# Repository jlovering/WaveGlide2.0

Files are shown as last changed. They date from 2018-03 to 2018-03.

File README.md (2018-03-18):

# WaveGlide 2.0

This project extends the work by [Nortd Labs](http://nortd.github.io/WaveGlide/). It seeks to take their work and simpify the board design.

This is intended as an Open Source Hardware ([OSHWA](https://www.oshwa.org)) project and will attempt to follow the OSHWA [Best Practices](https://www.oshwa.org/sharing-best-practices/). All parts of this design are released under CC-BY-SA 4.0 unless otherwise noted. See LICENSE.md for more details.

# Status
This project is in it's infancy. Current status is "Design Incomplete"

## Detailed Status
* EE Design
  * Component Selection: Complete
  * Schematic Capture: Incomplete
    * Power domains remain
  * Board Layout: Incomplete
    * Initial Floorplaning Started
  * Board Validation: Incomplete

* ME Design
  * ECAD Parts: Mostly Complete
  * MCAD Parts: Not Started
  * Assempbly Design: Not Started

 * Software Design: Not Started

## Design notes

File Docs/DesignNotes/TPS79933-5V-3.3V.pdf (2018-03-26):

## WEBENCH ® Design Report

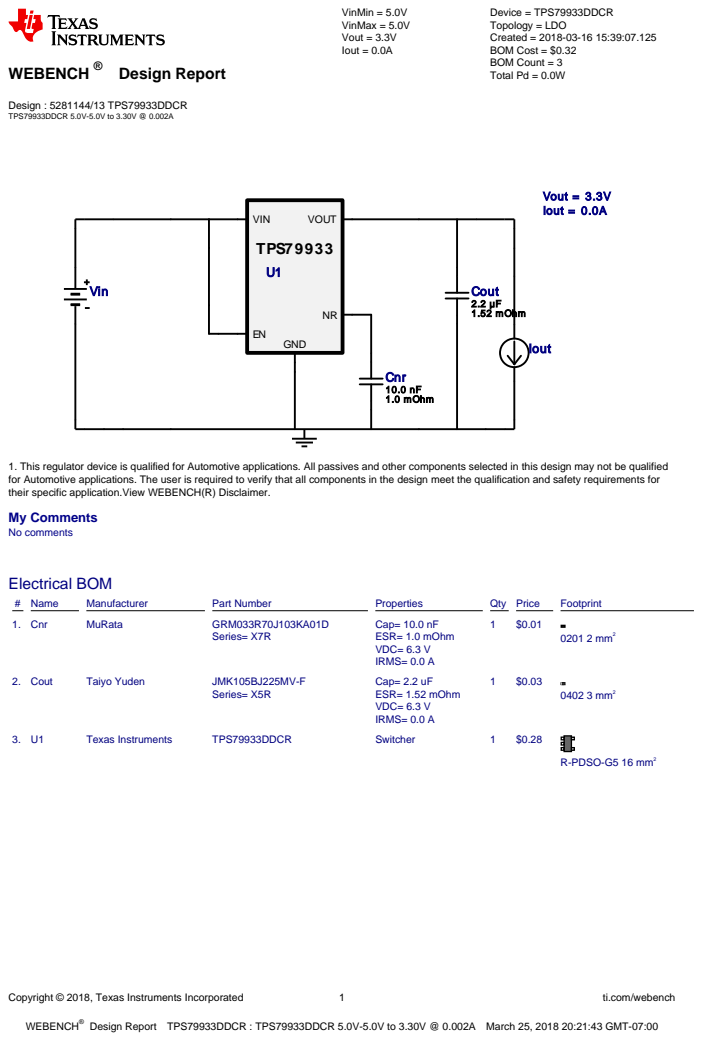
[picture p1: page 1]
Copyright © 2018, Texas Instruments Incorporated; ti.com/webench; WEBENCH®; Design : 5281144/13 TPS79933DDCR TPS79933DDCR 5.0V-5.0V to 3.30V @ 0.002A; VinMin = 5.0V VinMax = 5.0V Vout = 3.3V Iout = 0.0A; Device = TPS79933DDCR Topology = LDO Created = 2018-03-16 15:39:07.125 BOM Cost = $0.32 BOM Count = 3 Total Pd = 0.0W; Cnr 10.0 nF 1.0 mOhm; Cout 2.2 µF 1.52 mOhm; TPS79933; VIN; GND; VOUT; Vout = 3.3V Iout = 0.0A; Vin; Iout; Electrical BOM; # Name; Manufacturer; Part Number; Properties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

1. This regulator device is qualified for Automotive applications. All passives and other components selected in this design may not be qualified
for Automotive applications. The user is required to verify that all components in the design meet the qualification and safety requirements for
their specific application.View WEBENCH(R) Disclaimer.
My Comments
No comments

Design Report TPS79933DDCR : TPS79933DDCR 5.0V-5.0V to 3.30V @ 0.002A March 25, 2018 20:21:43 GMT-07:00

Design

Copyright © 2018, Texas Instruments Incorporated | 2 | ti.com/webench

Iin Avg

Vin= 5.0V

0.00025 0.00050 0.00075 0.00100 0.00125 0.00150 0.00175 0.00200 Output Current (A)

0.00000

0.00025

0.00050

0.00075

0.00100

0.00125

0.00150

0.00175

0.00200

Iin Avg(A)

Efficiency

Vin= 5.0V

0.00025 0.00050 0.00075 0.00100 0.00125 0.00150 0.00175 0.00200 Output Current (A)

45.0

47.5

50.0

52.5

55.0

57.5

60.0

62.5

65.0

Efficiency(%)

IC Pd

Vin= 5.0V

0.00025 0.00050 0.00075 0.00100 0.00125 0.00150 0.00175 0.00200 Output Current (A)

0.00025

0.00050

0.00075

0.00100

0.00125

0.00150

0.00175

0.00200

0.00225

0.00250

0.00275

0.00300

0.00325

0.00350

0.00375

IC Pd(W)

Total Pd

Vin= 5.0V

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

0.00025

0.00050

0.00075

0.00100

0.00125

0.00150

0.00175

0.00200

0.00225

0.00250

0.00275

0.00300

0.00325

0.00350

0.00375

Total Pd(W)

Pout

Vin= 5.0V

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

0.0000

0.0005

0.0010

0.0015

0.0020

0.0025

0.0030

0.0035

0.0040

0.0045

0.0050

0.0055

0.0060

0.0065

Pout(W)

IC Tj

Vin= 5.0V

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

30.05

30.10

30.15

30.20

30.25

30.30

30.35

30.40

30.45

30.50

30.55

30.60

30.65

30.70

30.75

30.80

IC Tj(degC)

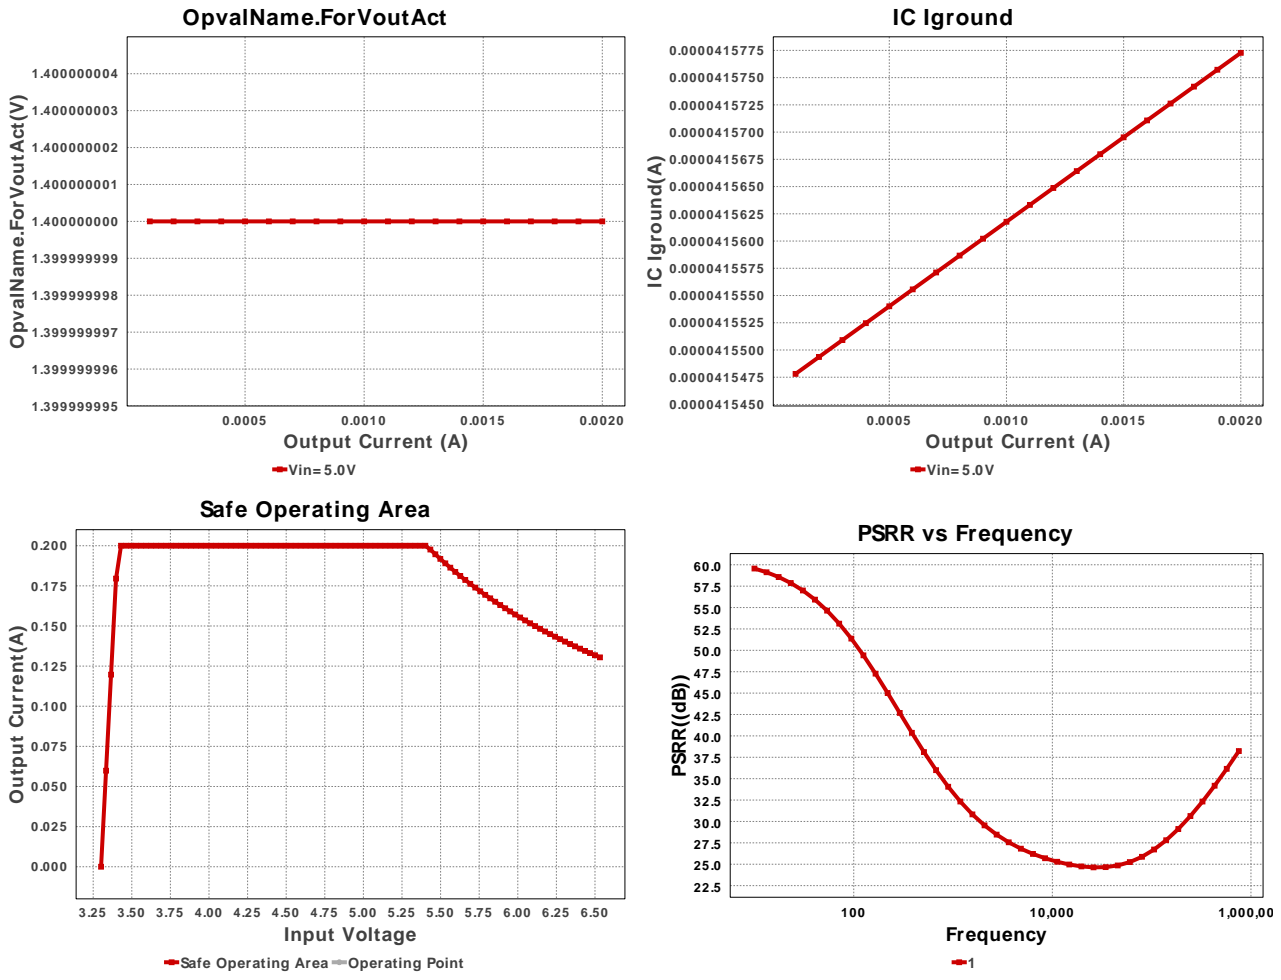
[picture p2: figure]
OpvalName.ForVoutAct; Vin= 5.0V; 0.0020 Output Current (A); OpvalName.ForVoutAct(V); IC Iground; IC Iground(A); Safe Operating Area; Safe Operating Area Operating Point; Input Voltage; Output Current(A); PSRR vs Frequency; 1,000,000 Frequency; PSRR((dB))

Copyright © 2018, Texas Instruments Incorporated | 3 | ti.com/webench

3.25 3.50 3.75 4.00 4.25 4.50 4.75 5.00 5.25 5.50 5.75 6.00 6.25 6.50

## Operating Values

# | Name | Value | Category | Description

1. IC Iground | 41.577 µA | Current | IC ground current
2. Iin Avg | 2.042 mA | Current | Average input current
3. BOM Count | 3 | General | Total Design BOM count
4. FootPrint | 21.0 mm² | General | Total Foot Print Area of BOM components
5. IC Tolerance | 66.0 mV | General | IC Feedback Tolerance
6. Output Noise RMS | 6.93 µV | General | Noise RMS
7. Pout | 6.6 mW | General | Total output power
8. Total BOM | $0.32 | General | Total BOM Cost
9. Efficiency | 64.656 % | Op Point | Steady state efficiency
10. IC Tj | 30.813 degC | Op Point | IC junction temperature
11. ICThetaJA | 225.3 degC/W | Op Point | IC junction-to-ambient thermal resistance
12. IOUT_OP | 2.0 mA | Op Point | Iout operating point
13. Input Ripple Frequency 100.0 kHz | Op Point | Input Source Ripple Frequency for PSRR Calculation
14. PSRR est. | -26.531 dB | Op Point | Power Supply Rejection Ratio estimated
15. VIN_OP | 5.0 V | Op Point | Vin operating point
16. Vin p-p | 50.0 mV | Op Point | Input Source ripple voltage
17. Vout OP | 3.3 V | Op Point | Operational Output Voltage
18. Vout Tolerance | 2.0 % | Op Point | Vout Tolerance based on IC Tolerance (no load) and voltage divider
| | | | resistors if applicable
19. Vout p-p | 2.357 mV | Op Point | Peak-to-peak output ripple voltage
20. IC Pd | 3.608 mW | Power | IC power dissipation
21. Total Pd | 3.608 mW | Power | Total Power Dissipation
22. Vout Act | 1.4 V | Achieved Vout with feedback resistor pair

## Design Inputs

# | Name | Value | Description

1. Iout | 2.0 m | Maximum Output Current
2. VinMax | 5.0 | Maximum input voltage
3. VinMin | 5.0 | Minimum input voltage
4. Vout | 3.3 | Output Voltage

Copyright © 2018, Texas Instruments Incorporated | 4 | ti.com/webench
# | Name | Value | Description

5. base_pn | TPS79933 | Base Product Number
6. source | DC | Input Source Type
7. Ta | 30.0 | Ambient temperature

## Design Assistance

1. TPS79933 Product Folder : http://www.ti.com/product/tps799 : contains the data sheet and other resources.

Texas Instruments' WEBENCH simulation tools attempt to recreate the performance of a substantially equivalent physical implementation
of the design. Simulations are created using Texas Instruments' published specifications as well as the published specifications of other device manufacturers. While Texas Instruments does update this information periodically, this information may not be current at the time the simulation is built. Texas Instruments does not warrant the accuracy or completeness of the specifications or any information contained therein. Texas Instruments does not warrant that any designs or recommended parts will meet the specifications you entered, will be suitable for your application or fit for any particular purpose, or will operate as shown in the simulation in a physical implementation. Texas Instruments does not warrant that the designs are production worthy.
You should completely validate and test your design implementation to confirm the system functionality for your application prior to production.
Use of Texas Instruments' WEBENCH simulation tools is subject to Texas Instruments' Site Terms and Conditions of Use. (http://www.ti.com/corp/docs/legal/termsofuse.shtml) Prototype boards based on WEBENCH created designs are provided AS IS without warranty of any kind for evaluation and testing purposes and are subject to the terms of the Evaluation License Agreement. (http://www.ti.com/corp/docs/legal/termsofuse_estore.shtml)

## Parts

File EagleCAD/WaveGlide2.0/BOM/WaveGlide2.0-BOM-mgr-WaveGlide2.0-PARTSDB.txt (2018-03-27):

Mfg Part Num	Mfg Name	VID	Vendor Part Num	Description	Pkg Code
N/A	N/A	DO NOT PLACE	DO NOT PLACE	*	*
N/A	N/A	TO BE DETERMINED	TO BE DETERMINED	*	*
ANY	ANY	ANY	ANY	ANY PART MATCHING	*
08053C104JAZ2A	AVX	TO BE DETERMINED	TO BE DETERMINED	CAP CER 0.1UF 25V X7R 0805	0805
GCM2195C1H103JA16D	MuRata	TO BE DETERMINED	TO BE DETERMINED	CAP CER 10000PF 50V C0G/NP0 0805	0805
GRM219R61A106KE44D	MuRata	TO BE DETERMINED	TO BE DETERMINED	CAP CER 10UF 10V X5R 0805	0805
CC0805KRX7R8BB104	Yageo America	TO BE DETERMINED	TO BE DETERMINED	CAP CER 0.1UF 25V X7R 0805	0805
GRM32ER61C226ME20L	MuRata	TO BE DETERMINED	TO BE DETERMINED	CAP CER 22UF 16V X5R 1210	1210
GRM155R60J223KA01D	MuRata	TO BE DETERMINED	TO BE DETERMINED	CAP CER 0.022UF 6.3V X5R 0402	0402
MBRD835LT4G	ON Semiconductor	TO BE DETERMINED	TO BE DETERMINED	DIODE SCHOTTKY 35V 8A DPAK	DPAK
XAL5030-332MEB	Coilcraft	TO BE DETERMINED	TO BE DETERMINED	FIXED IND 33UH 5.9A 21MOHM	XAL5030
RR1220P-103-D	Susumu Co Ltd	TO BE DETERMINED	TO BE DETERMINED	RES SMD 10K OHM 0.5% 1/10W 0805	0805
CRCW0603953RFKEA	Vishay-Dale	TO BE DETERMINED	TO BE DETERMINED	RES SMD 953 OHM 1% 1/10W 0603	0603
CRCW060386K6FKEA	Vishay-Dale	TO BE DETERMINED	TO BE DETERMINED	RES SMD 86.6K OHM 1% 1/10W 0603	0603
CRCW060360K4FKEA	Vishay-Dale	TO BE DETERMINED	TO BE DETERMINED	RES SMD 60.4K OHM 1% 1/10W 0603	0603
TPS55340RTER	Texas Instruments	TO BE DETERMINED	TO BE DETERMINED	IC REG MULT CONFG ISO ADJ 16WQFN	S-PWQFN-N16
EMK107B7105KA-T	Taiyo Yuden	TO BE DETERMINED	TO BE DETERMINED	CAP CER 1UF 16V X7R 0603	0603
GRM21BR60J106ME19L	MuRata	TO BE DETERMINED	TO BE DETERMINED	CAP CER 10UF 6.3V X5R 0805	0805
C0805C106K8PACTU	Kemet	TO BE DETERMINED	TO BE DETERMINED	CAP CER 10UF 10V X5R 0805	0805
LQM2HPN4R7MGCL	MuRata	TO BE DETERMINED	TO BE DETERMINED	FIXED IND 4.7UH 800MA 180MOHM	1008
TPS61222DCKR	Texas Instruments	TO BE DETERMINED	TO BE DETERMINED	IC REG BOOST 5V 0.2A SYNC SC70-6	SC70-6
GRM188R60J475KE19D	MuRata	TO BE DETERMINED	TO BE DETERMINED	CAP CER 4.7UF 6.3V X5R 0603	0603
06035A470KAT2A	ATK	TO BE DETERMINED	TO BE DETERMINED	CAP CER 47PF 50V C0G/NP0 0603	0603
CRCW06031M50FKEA	Vishay-Dale	TO BE DETERMINED	TO BE DETERMINED	RES SMD 1.5M OHM 1% 1/10W 0603	0603
CRCW0603158KFKEA	Vishay-Dale	TO BE DETERMINED	TO BE DETERMINED	RES SMD 158K OHM 1% 1/10W 0603	0603
GMK212B7105KG	Taiyo Yuden	TO BE DETERMINED	TO BE DETERMINED	CAP CER 1UF 35V X7R 0805	0805
TPS61041DBVR	Texas Instruments	TO BE DETERMINED	TO BE DETERMINED	IC LED DRIVER RGLTR DIM SOT23-5	SOT23-5
LPS4018-183MRB	Coilcraft	TO BE DETERMINED	TO BE DETERMINED	FIXED IND 18UH 700MA 270MOHM	LPS4018
TPS79933DDCR	Texas Instruments	TO BE DETERMINED	TO BE DETERMINED	IC REG LINEAR 3.3V 200MA SOT23-5	SOT23-5
GRM155R70J103KA01D	MuRata	TO BE DETERMINED	TO BE DETERMINED	CAP CER 10000PF 6.3V X7R 0402	0402
JMK105BJ225MV-F	Taiyo Yuden	TO BE DETERMINED	TO BE DETERMINED	CAP CER 2.2UF 6.3V X5R 0402	0402
MBR1020VL	Fairchild Semiconductor	TO BE DETERMINED	TO BE DETERMINED	DIODE SCHOTTKY 20V 1A SOD123F	SOD-123F

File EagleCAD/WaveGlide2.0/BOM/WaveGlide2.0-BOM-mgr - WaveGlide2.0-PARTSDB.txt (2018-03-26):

Mfg Part Num	Mfg Name	VID	Vendor Part Num	Description	Pkg Code
N/A	N/A	DO NOT PLACE	DO NOT PLACE	*	*
N/A	N/A	TO BE DETERMINED	TO BE DETERMINED	*	*
08053C104JAZ2A	AVX	TO BE DETERMINED	TO BE DETERMINED	*	0805
GCM2195C1H103JA16D	MuRata	TO BE DETERMINED	TO BE DETERMINED	*	0805
GRM219R61A106KE44D	MuRata	TO BE DETERMINED	TO BE DETERMINED	*	0805
CC0805KRX7R8BB104	Yageo America	TO BE DETERMINED	TO BE DETERMINED	*	0805
GRM32ER61C226ME20L	MuRata	TO BE DETERMINED	TO BE DETERMINED	*	1210
GRM033R60J223KE01D	MuRata	TO BE DETERMINED	TO BE DETERMINED	*	0201
MBRD835LT4G	ON Semiconductor	TO BE DETERMINED	TO BE DETERMINED	*	DPAK
XAL5030-332MEB	Coilcraft	TO BE DETERMINED	TO BE DETERMINED	*	XAL5030
CRCW0402953RFKED	Vishay-Dale	TO BE DETERMINED	TO BE DETERMINED	*	0402
RR1220P-103-D	Susumu Co Ltd	TO BE DETERMINED	TO BE DETERMINED	*	0805
CRCW040286K6FKED	Vishay-Dale	TO BE DETERMINED	TO BE DETERMINED	*	0402
CRCW040260K4FKED	Vishay-Dale	TO BE DETERMINED	TO BE DETERMINED	*	0402
TPS55340RTER	Texas Instruments	TO BE DETERMINED	TO BE DETERMINED	*	S-PWQFN-N16
EMK107B7105KA-T	Taiyo Yuden	TO BE DETERMINED	TO BE DETERMINED	*	0603
GRM21BR60J106ME19L	MuRata	TO BE DETERMINED	TO BE DETERMINED	CAP CER 10UF 6.3V X5R 0805	0805
C0805C106K8PACTU	Kemet	TO BE DETERMINED	TO BE DETERMINED	*	0805
LQM2HPN4R7MGCL	MuRata	TO BE DETERMINED	TO BE DETERMINED	CAP CER 10UF 10V X5R 0805	1008
TPS61222DCKR	Texas Instruments	TO BE DETERMINED	TO BE DETERMINED	*	DCK6

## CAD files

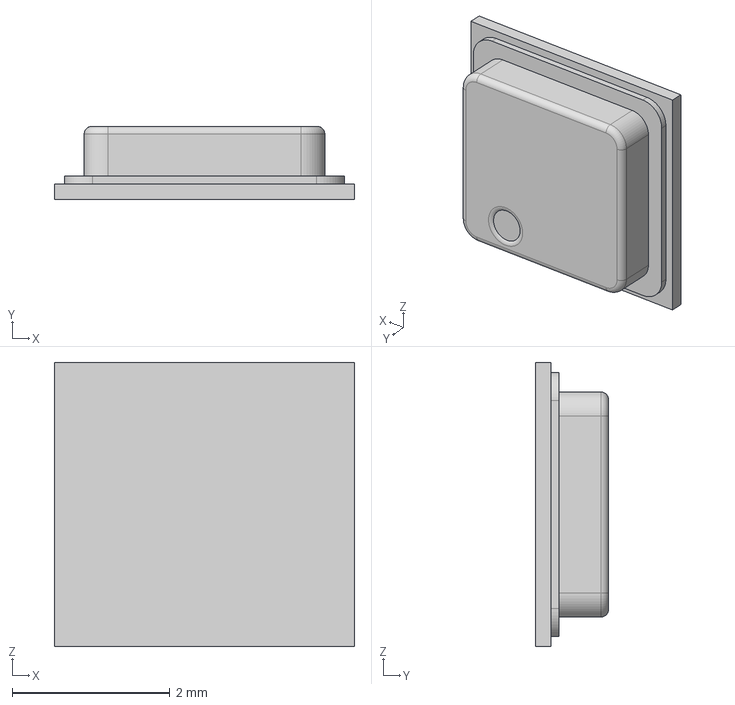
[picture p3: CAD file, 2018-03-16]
MCAD/BMP180.step
3.80 x 0.93 x 3.60 mm

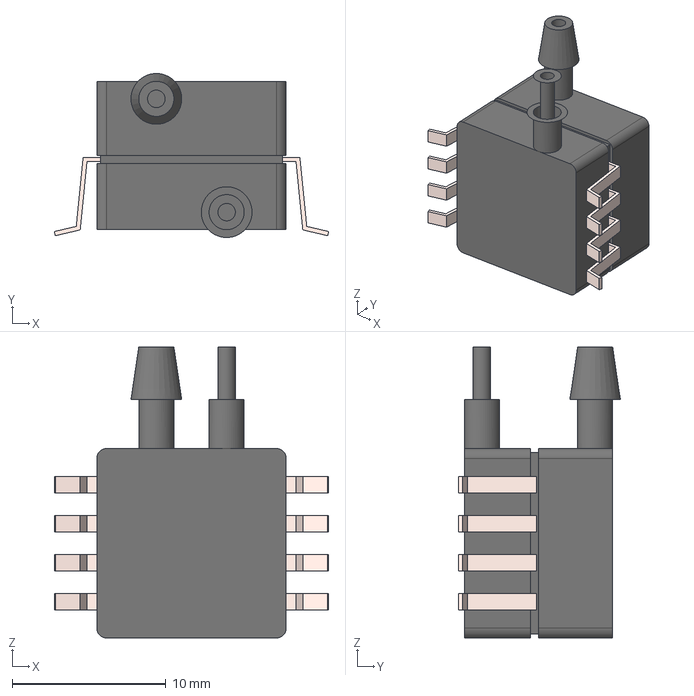
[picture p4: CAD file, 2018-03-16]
MCAD/MPXV7002.step
17.8 x 10.7 x 18.9 mm

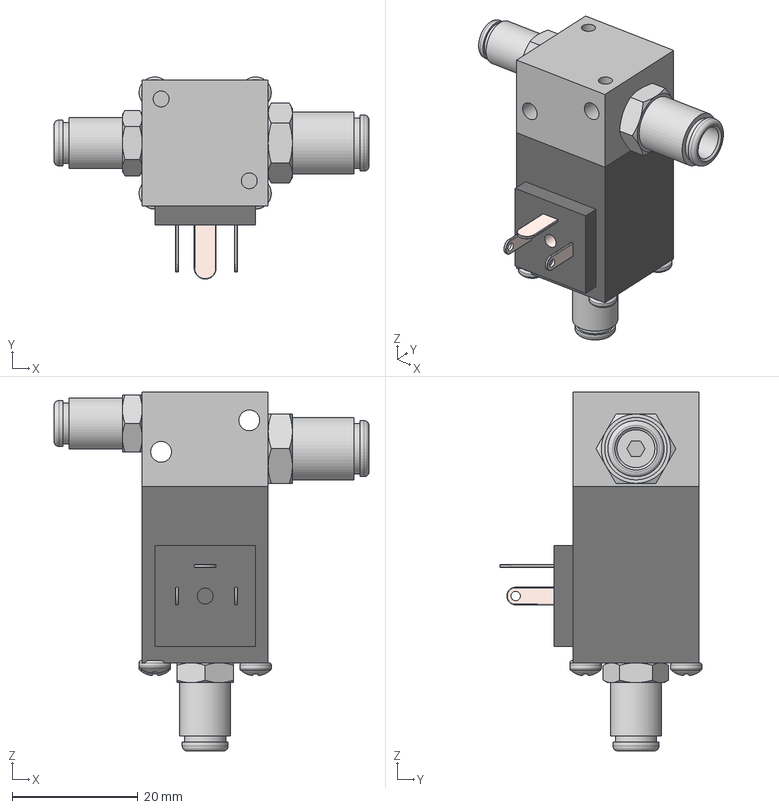
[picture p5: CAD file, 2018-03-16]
MCAD/GB-MS-20 + Press Fits v3.step
50.0 x 32.1 x 57.0 mm
4mm/M5 press connect x 2
M2.5x30 x 4
Solenoid
Valve
6mm press connect

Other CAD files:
MCAD/GB-MS-20 + Press Fits v2.step

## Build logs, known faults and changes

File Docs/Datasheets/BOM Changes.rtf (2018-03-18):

BOM

Sub:
M5-4mm quick-connect with
M5-6mm quick connect (https://www.landefeld.de/artikel/en/straight-push-in-fitting-m-5-6mm-iqs-standard-m-hexagon-socket-/IQSG%20M56%20I)
OPTION M4-6mm quick-connect (https://www.mcmaster.com/#5225k506/=1bxlk7a)

M5 threaded nozzle (https://www.landefeld.de/artikel/en/threaded-nozzle-m-5-4mm-16-bar-brass/GT%2054%20MS)

OPTION M5-4mm quick-connect (https://www.mcmaster.com/#5225k503/=1bxlj6a)

1N4004 with
CGRM4004-G (https://ca.mouser.com/ProductDetail/Comchip-Technology/CGRM4004-G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)

Adafruit 1944 with:
BQ21040 (charger) (http://www.ti.com/product/bq21040)
TPS61222 (5V booster) (http://www.ti.com/product/TPS61220)
~~bq27441-G1 (fuel gauge) (http://www.ti.com/product/bq27441-g1)

PTN04050CAD with
TPS55340 (12V boost) (http://www.ti.com/lit/ds/symlink/tps55340.pdf)

Add:
TPS79933 (3.3V LDO) (http://www.ti.com/product/TPS709) [TPS707 PINOUT identical]
TPS61041 (13.5V boost) (http://www.ti.com/lit/ds/symlink/tps61041.pdf)
MC33502 (rail-rail op-amp) (https://www.onsemi.com/pub/Collateral/MC33502-D.PDF)
- This part works with the 5V->3.3V voltage divider to provide a clean 3.3V signal into the ADC without much fuss.

Remove
AQY212GH - Control boost via enable pin

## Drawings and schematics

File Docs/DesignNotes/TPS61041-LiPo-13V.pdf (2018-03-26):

## WEBENCH ® Design Report

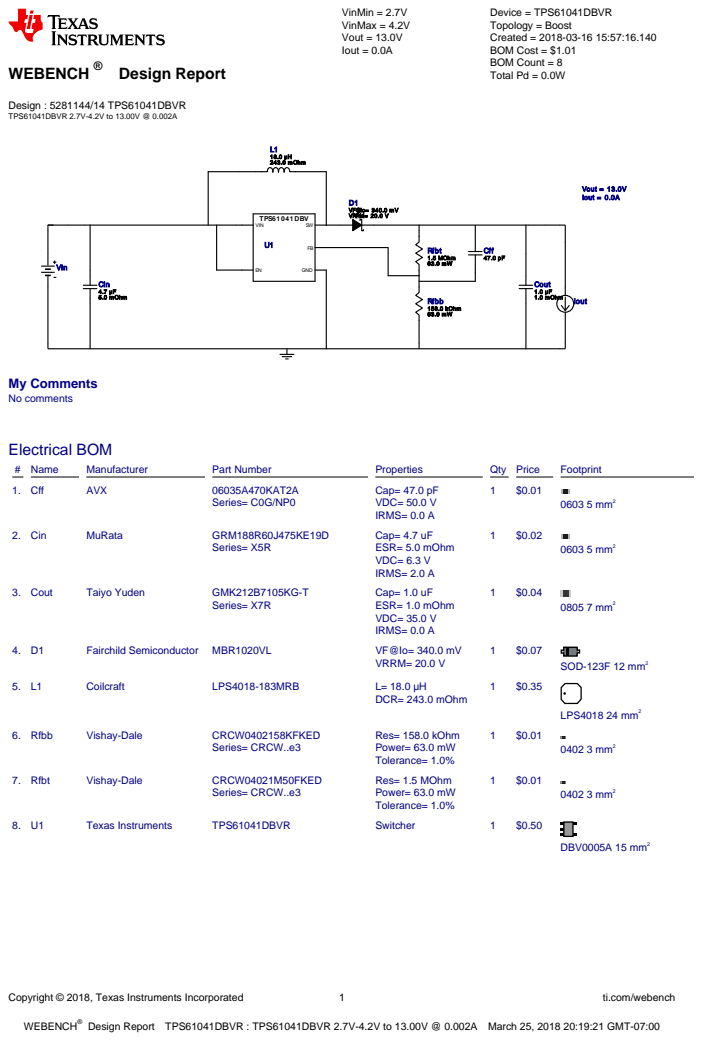
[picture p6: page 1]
Copyright © 2018, Texas Instruments Incorporated; ti.com/webench; WEBENCH®; Design : 5281144/14 TPS61041DBVR TPS61041DBVR 2.7V-4.2V to 13.00V @ 0.002A; VinMin = 2.7V VinMax = 4.2V Vout = 13.0V Iout = 0.0A; Device = TPS61041DBVR Topology = Boost Created = 2018-03-16 15:57:16.140 BOM Cost = $1.01 BOM Count = 8 Total Pd = 0.0W; Cin 4.7 µF 5.0 mOhm; Cout 1.0 µF 1.0 mOhm; D1 VF@Io= 340.0 mV VRRM= 20.0 V; L1 18.0 µH 243.0 mOhm; TPS61041DBV; GND; VIN; Vout = 13.0V Iout = 0.0A; Cff 47.0 pF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

Design Report TPS61041DBVR : TPS61041DBVR 2.7V-4.2V to 13.00V @ 0.002A March 25, 2018 20:19:21 GMT-07:00

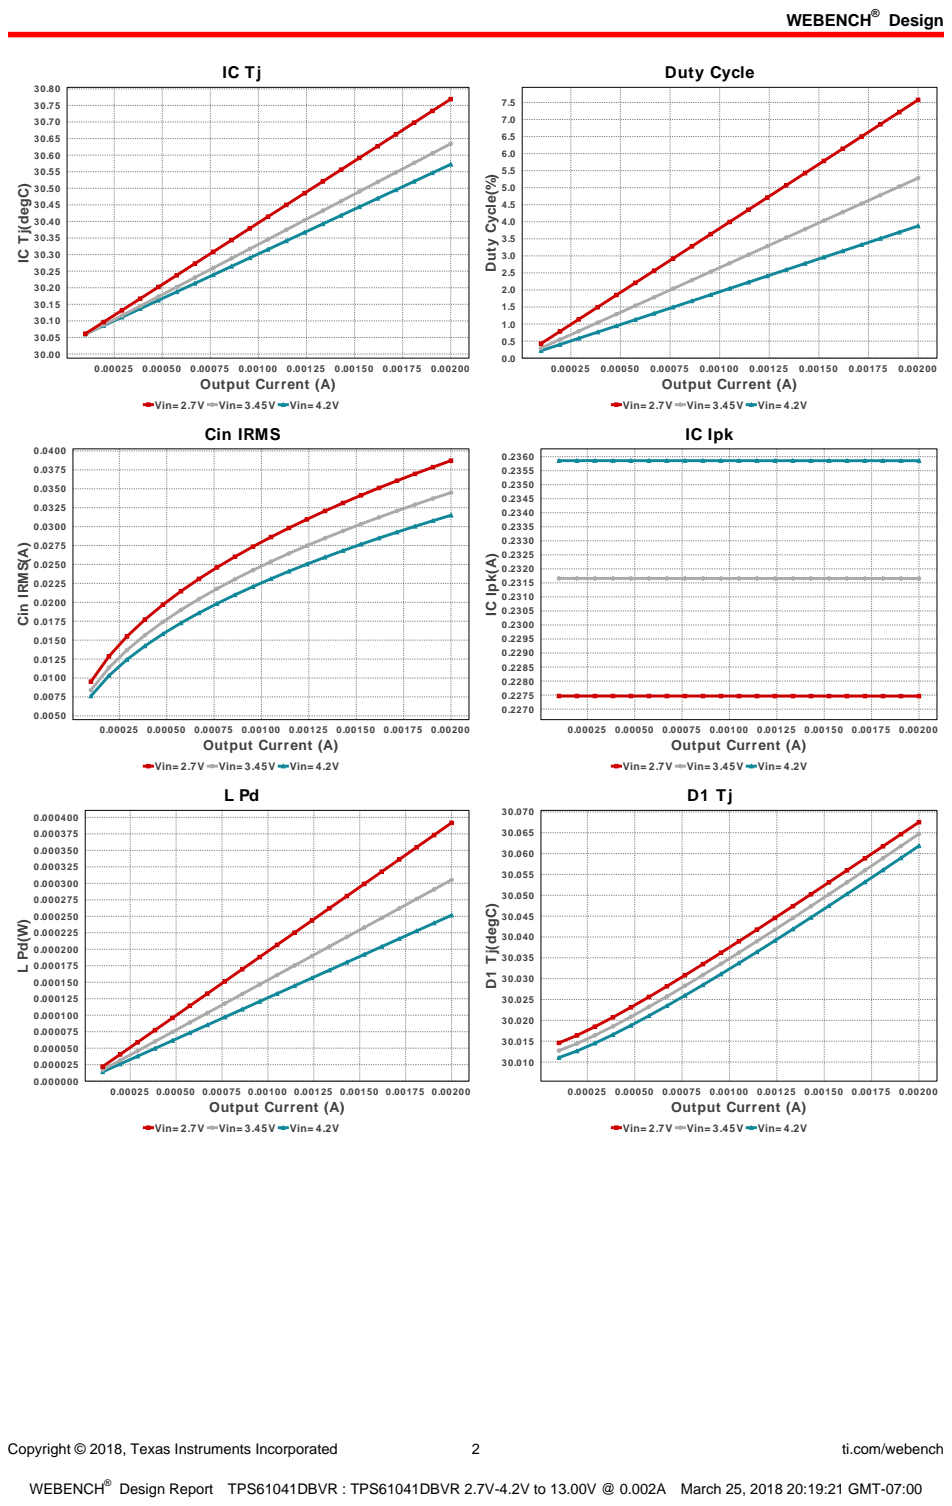
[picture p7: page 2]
Design; Copyright © 2018, Texas Instruments Incorporated; ti.com/webench; 0.00025 0.00050 0.00075 0.00100 0.00125 0.00150 0.00175 0.00200 Output Current (A); Duty Cycle; Duty Cycle(%); Cin IRMS(A); IC Ipk; IC Ipk(A); D1 Tj(degC)

IC Tj(degC)

Vin= 2.7V Vin= 3.45V Vin= 4.2V
Cin IRMS

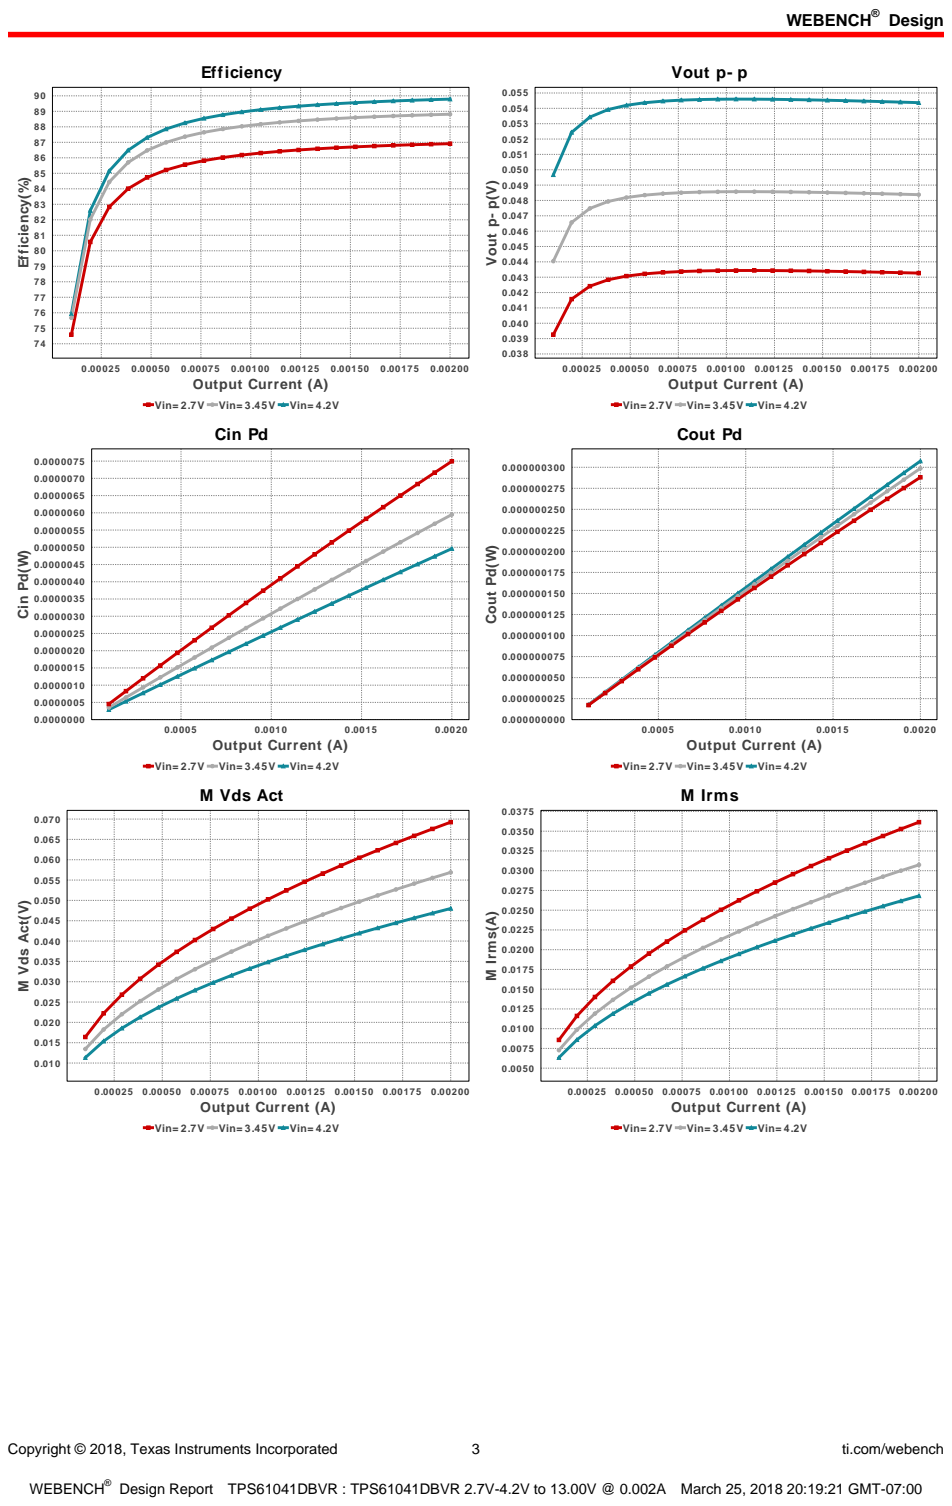
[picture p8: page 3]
Copyright © 2018, Texas Instruments Incorporated; ti.com/webench; Efficiency; 0.00025 0.00050 0.00075 0.00100 0.00125 0.00150 0.00175 0.00200 Output Current (A); Efficiency(%); Vout p- p; Vout p- p(V); Cin Pd; 0.0020 Output Current (A); Cin Pd(W); Cout Pd(W); M Vds Act(V); M Irms; M Irms(A)

Vin= 2.7V Vin= 3.45V Vin= 4.2V

Cout Pd

M Vds Act

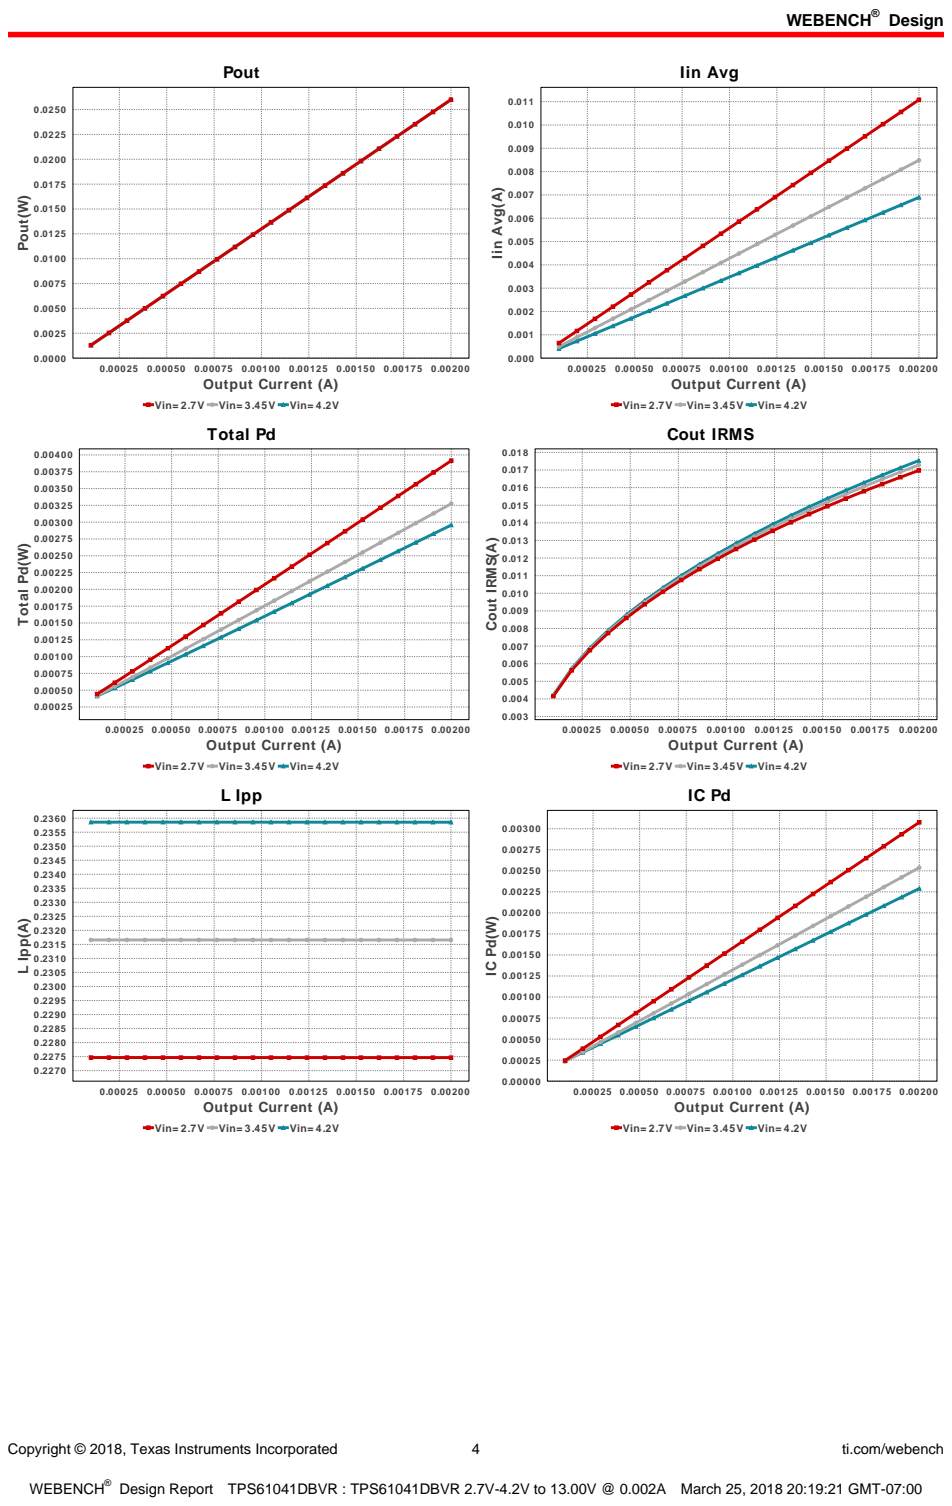
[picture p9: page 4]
Copyright © 2018, Texas Instruments Incorporated; ti.com/webench; Pout; 0.00025 0.00050 0.00075 0.00100 0.00125 0.00150 0.00175 0.00200 Output Current (A); Pout(W); Iin Avg; Iin Avg(A); Total Pd(W); Cout IRMS(A); L Ipp; L Ipp(A)

Vin= 2.7V Vin= 3.45V Vin= 4.2V
Total Pd

Cout IRMS

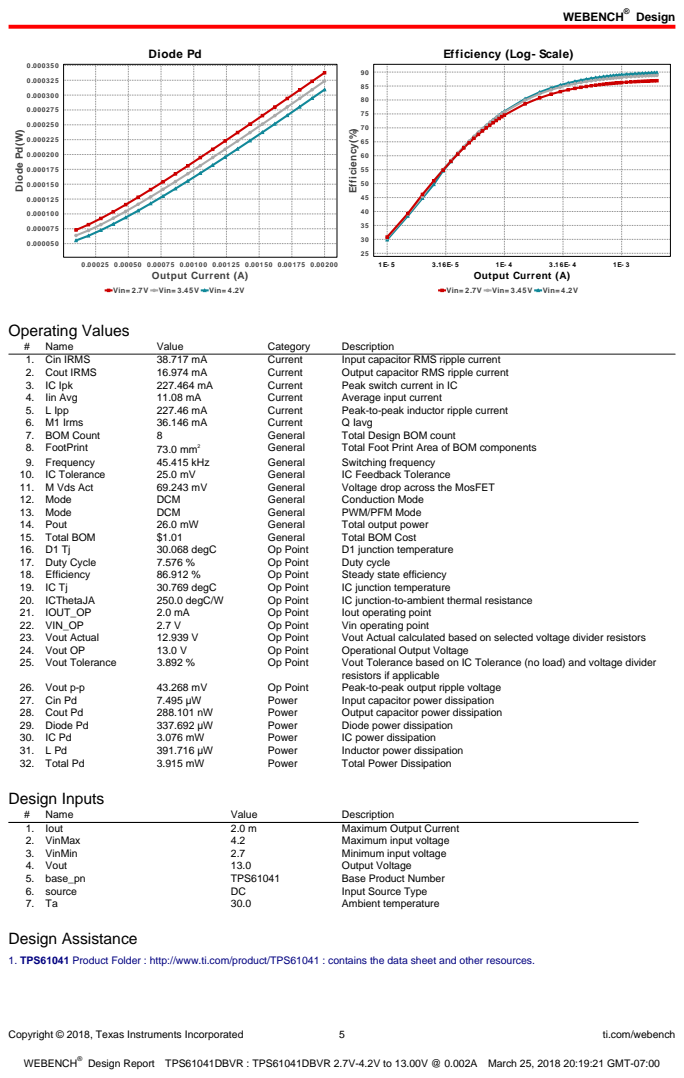
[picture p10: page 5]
Copyright © 2018, Texas Instruments Incorporated; ti.com/webench; Diode Pd; 0.00025 0.00050 0.00075 0.00100 0.00125 0.00150 0.00175 0.00200 Output Current (A); Diode Pd(W); 1E- 3 Output Current (A); Efficiency(%); Operating Values; Name; Value; Category; Description; 1. Cin IRMS; Current; Input capacitor RMS ripple current; 2. Cout IRMS; Output capacitor RMS ripple current; 3. IC Ipk; Peak switch current in IC; 4. Iin Avg; Average input current; 5. L Ipp; Peak-to-peak inductor ripple current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

Efficiency (Log- Scale)

Vin= 2.7V Vin= 3.45V Vin= 4.2V

resistors if applicable

1. TPS61041 Product Folder : http://www.ti.com/product/TPS61041 : contains the data sheet and other resources.

Copyright © 2018, Texas Instruments Incorporated | 6 | ti.com/webench

Texas Instruments' WEBENCH simulation tools attempt to recreate the performance of a substantially equivalent physical implementation
of the design. Simulations are created using Texas Instruments' published specifications as well as the published specifications of other device manufacturers. While Texas Instruments does update this information periodically, this information may not be current at the time the simulation is built. Texas Instruments does not warrant the accuracy or completeness of the specifications or any information contained therein. Texas Instruments does not warrant that any designs or recommended parts will meet the specifications you entered, will be suitable for your application or fit for any particular purpose, or will operate as shown in the simulation in a physical implementation. Texas Instruments does not warrant that the designs are production worthy.
You should completely validate and test your design implementation to confirm the system functionality for your application prior to production.
Use of Texas Instruments' WEBENCH simulation tools is subject to Texas Instruments' Site Terms and Conditions of Use. (http://www.ti.com/corp/docs/legal/termsofuse.shtml) Prototype boards based on WEBENCH created designs are provided AS IS without warranty of any kind for evaluation and testing purposes and are subject to the terms of the Evaluation License Agreement. (http://www.ti.com/corp/docs/legal/termsofuse_estore.shtml)

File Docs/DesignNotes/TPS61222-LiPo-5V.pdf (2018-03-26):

## WEBENCH ® Design Report

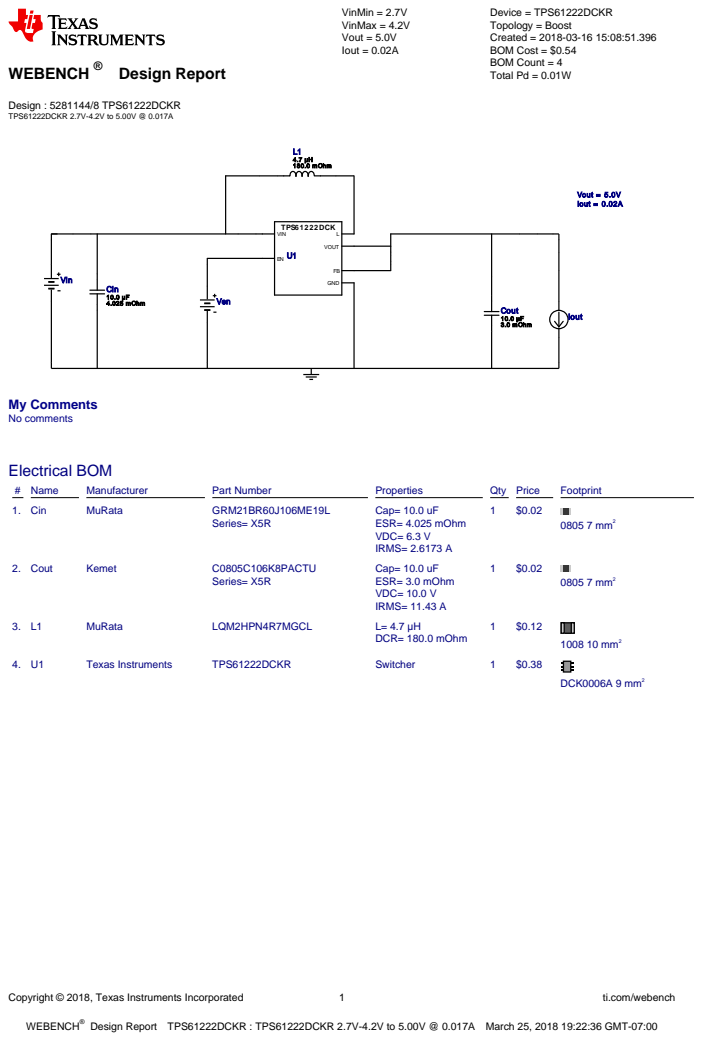
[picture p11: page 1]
Copyright © 2018, Texas Instruments Incorporated; ti.com/webench; WEBENCH®; Design : 5281144/8 TPS61222DCKR TPS61222DCKR 2.7V-4.2V to 5.00V @ 0.017A; VinMin = 2.7V VinMax = 4.2V Vout = 5.0V Iout = 0.02A; Device = TPS61222DCKR Topology = Boost Created = 2018-03-16 15:08:51.396 BOM Cost = $0.54 BOM Count = 4 Total Pd = 0.01W; Cin 10.0 µF; 4.025 mOhm; Cout; 10.0 µF 3.0 mOhm; L1 4.7 µH 180.0 mOhm; TPS61222DCK VIN; GND; VOUT; Vout = 5.0V Iout = 0.02A; Ven; Vin; Iout; My Comments No comments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

Design Report TPS61222DCKR : TPS61222DCKR 2.7V-4.2V to 5.00V @ 0.017A March 25, 2018 19:22:36 GMT-07:00

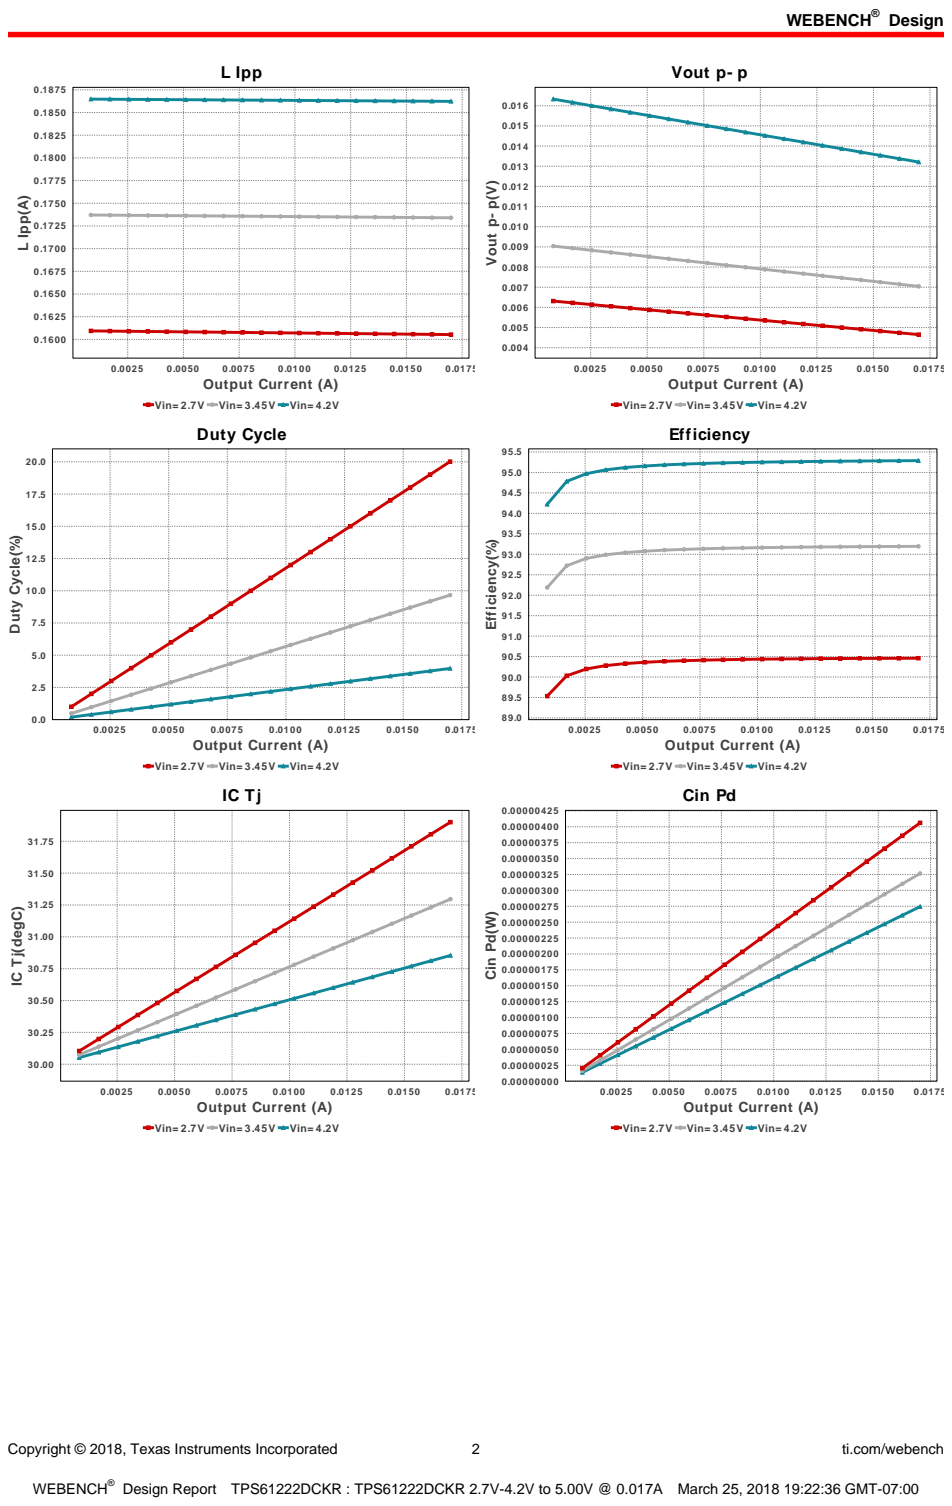
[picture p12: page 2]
Design; Copyright © 2018, Texas Instruments Incorporated; ti.com/webench; L Ipp; 0.0175 Output Current (A); L Ipp(A); Vout p- p; Vout p- p(V); Duty Cycle(%); Efficiency(%); Cin Pd; Cin Pd(W)

Vin= 2.7V Vin= 3.45V Vin= 4.2V
Duty Cycle

Efficiency

IC Tj(degC)

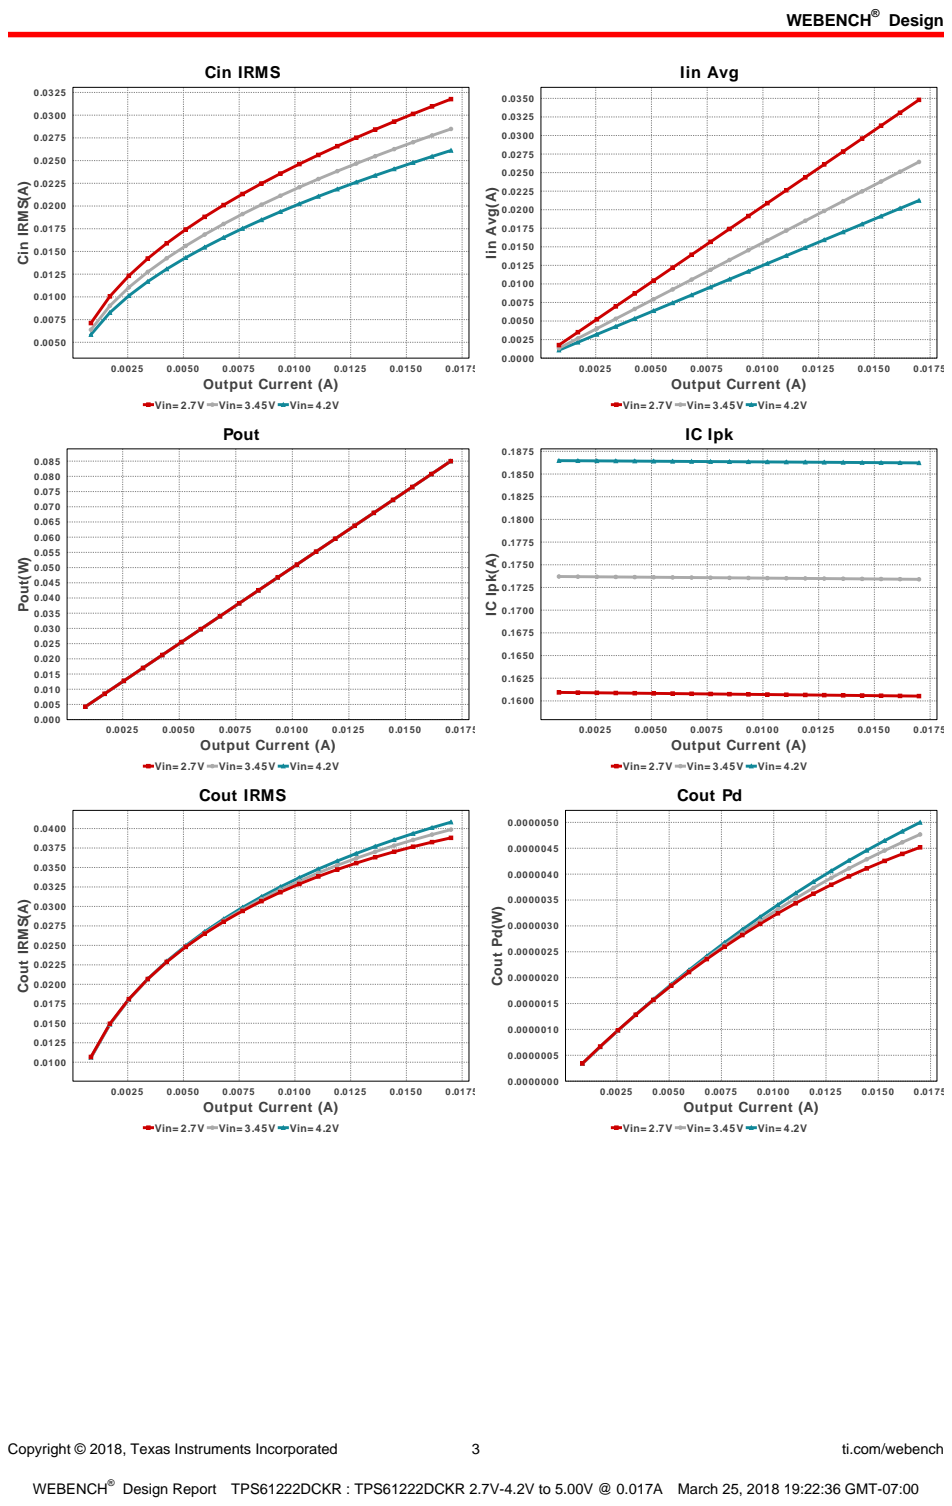
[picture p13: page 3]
Copyright © 2018, Texas Instruments Incorporated; ti.com/webench; Cin IRMS; 0.0175 Output Current (A); Cin IRMS(A); Iin Avg; Iin Avg(A); Pout; Pout(W); IC Ipk; IC Ipk(A); Cout IRMS(A); Cout Pd(W)

Vin= 2.7V Vin= 3.45V Vin= 4.2V

Cout IRMS

Cout Pd

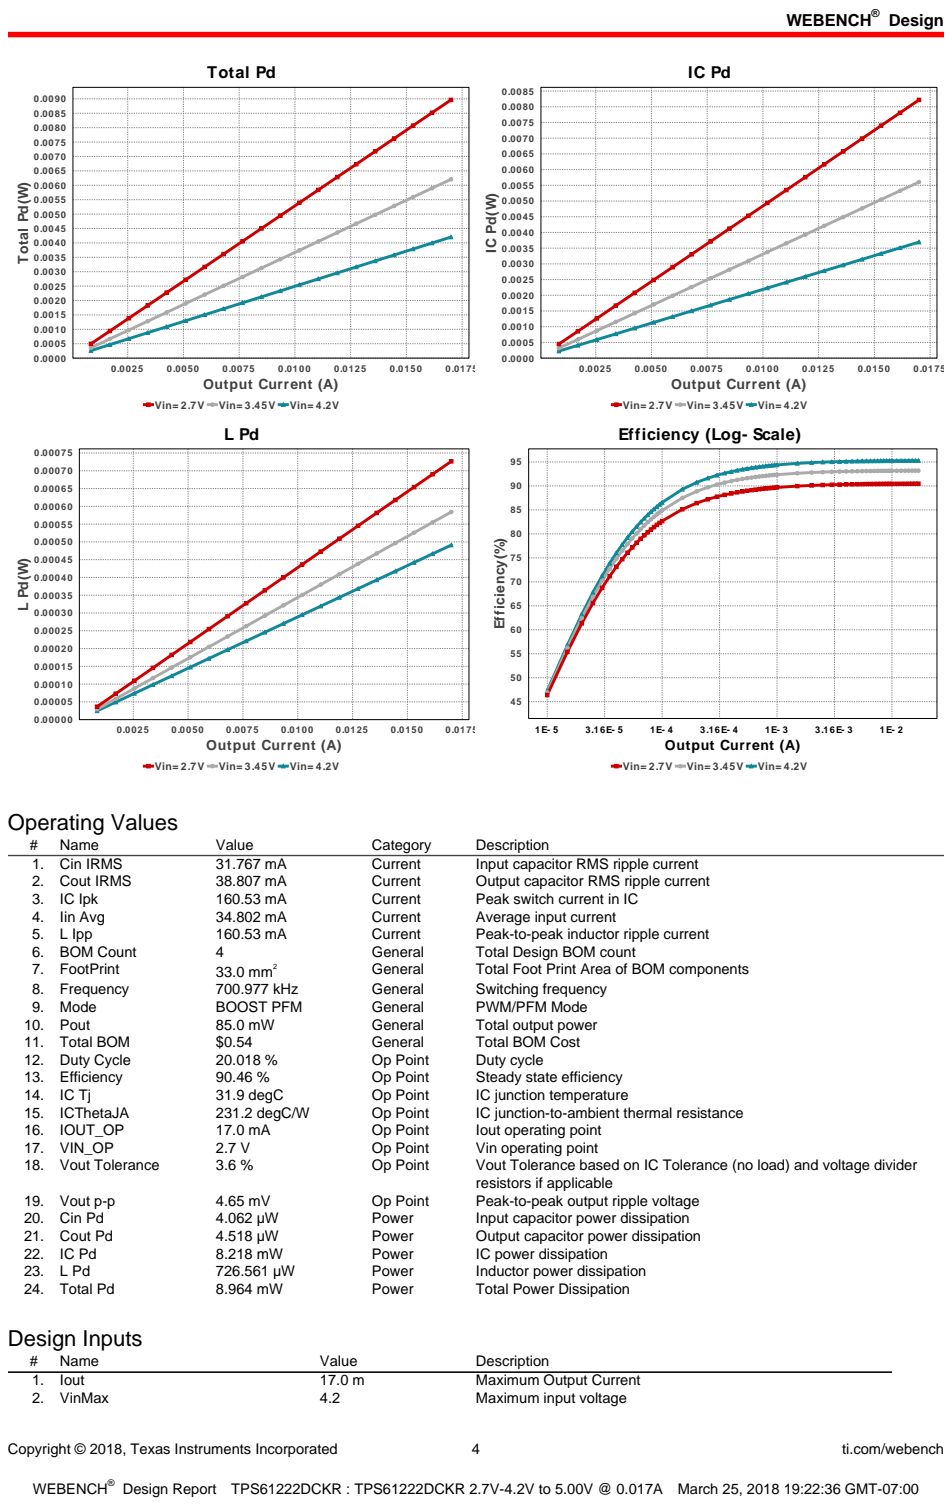
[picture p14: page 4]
Copyright © 2018, Texas Instruments Incorporated; ti.com/webench; Total Pd; 0.0175 Output Current (A); Total Pd(W); 1E- 2 Output Current (A); Efficiency(%); Operating Values; Name; Value; Category; Description; 1. Cin IRMS; Current; Input capacitor RMS ripple current; 2. Cout IRMS; Output capacitor RMS ripple current; 3. IC Ipk; Peak switch current in IC; 4. Iin Avg; Average input current; 5. L Ipp; Peak-to-peak inductor ripple current; 6. BOM Count; General; Total Design BOM count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

Vin= 2.7V Vin= 3.45V Vin= 4.2V

Efficiency (Log- Scale)

resistors if applicable

Copyright © 2018, Texas Instruments Incorporated | 5 | ti.com/webench
# | Name | Value | Description

3. VinMin | 2.7 | Minimum input voltage
4. Vout | 5.0 | Output Voltage
5. base_pn | TPS61222 | Base Product Number
6. source | DC | Input Source Type
7. Ta | 30.0 | Ambient temperature

## Design Assistance

1. TPS61222 Product Folder : http://www.ti.com/product/TPS61222 : contains the data sheet and other resources.

Texas Instruments' WEBENCH simulation tools attempt to recreate the performance of a substantially equivalent physical implementation
of the design. Simulations are created using Texas Instruments' published specifications as well as the published specifications of other device manufacturers. While Texas Instruments does update this information periodically, this information may not be current at the time the simulation is built. Texas Instruments does not warrant the accuracy or completeness of the specifications or any information contained therein. Texas Instruments does not warrant that any designs or recommended parts will meet the specifications you entered, will be suitable for your application or fit for any particular purpose, or will operate as shown in the simulation in a physical implementation. Texas Instruments does not warrant that the designs are production worthy.
You should completely validate and test your design implementation to confirm the system functionality for your application prior to production.
Use of Texas Instruments' WEBENCH simulation tools is subject to Texas Instruments' Site Terms and Conditions of Use. (http://www.ti.com/corp/docs/legal/termsofuse.shtml) Prototype boards based on WEBENCH created designs are provided AS IS without warranty of any kind for evaluation and testing purposes and are subject to the terms of the Evaluation License Agreement. (http://www.ti.com/corp/docs/legal/termsofuse_estore.shtml)

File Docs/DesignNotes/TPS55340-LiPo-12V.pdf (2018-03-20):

## WEBENCH ® Design Report

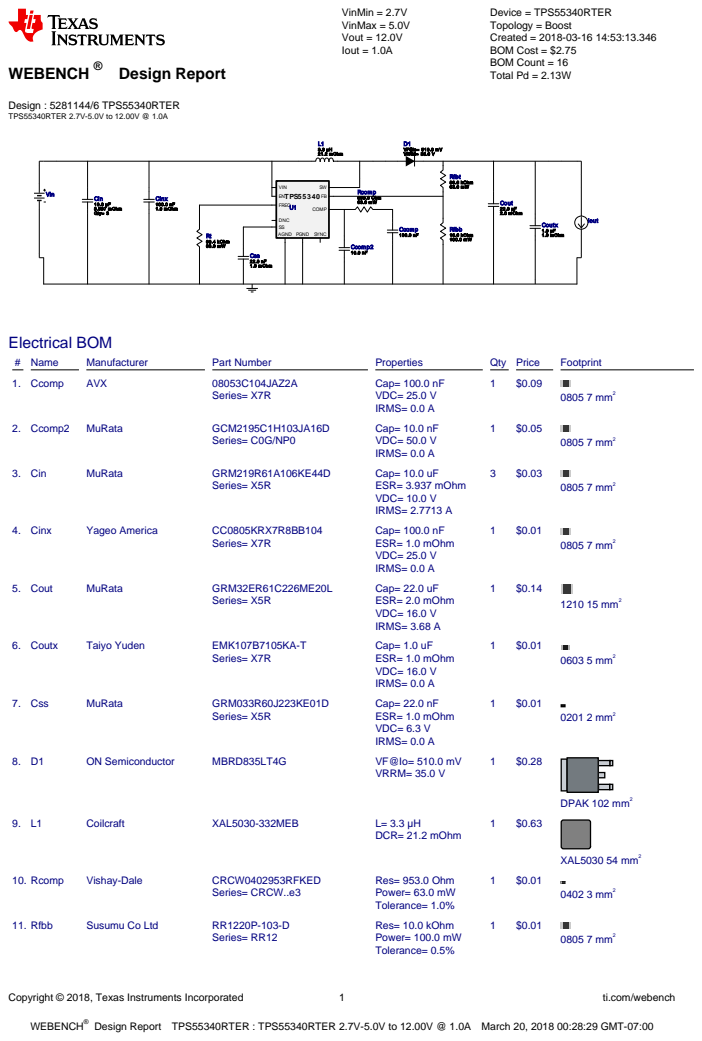
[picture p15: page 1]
Copyright © 2018, Texas Instruments Incorporated; ti.com/webench; WEBENCH®; Design : 5281144/6 TPS55340RTER TPS55340RTER 2.7V-5.0V to 12.00V @ 1.0A; VinMin = 2.7V VinMax = 5.0V Vout = 12.0V Iout = 1.0A; Device = TPS55340RTER Topology = Boost Created = 2018-03-16 14:53:13.346 BOM Cost = $2.75 BOM Count = 16 Total Pd = 2.13W; Ccomp 100.0 nF; Ccomp2 10.0 nF; Cin 10.0 µF 3.937 mOhm Qty= 3; Cinx 100.0 nF; 1.0 mOhm; Cout 22.0 µF; 2.0 mOhm; Css 22.0 nF 1.0 mOhm; D1 VF@Io= 510.0 mV VRRM= 35.0 V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

Design Report TPS55340RTER : TPS55340RTER 2.7V-5.0V to 12.00V @ 1.0A March 20, 2018 00:28:29 GMT-07:00

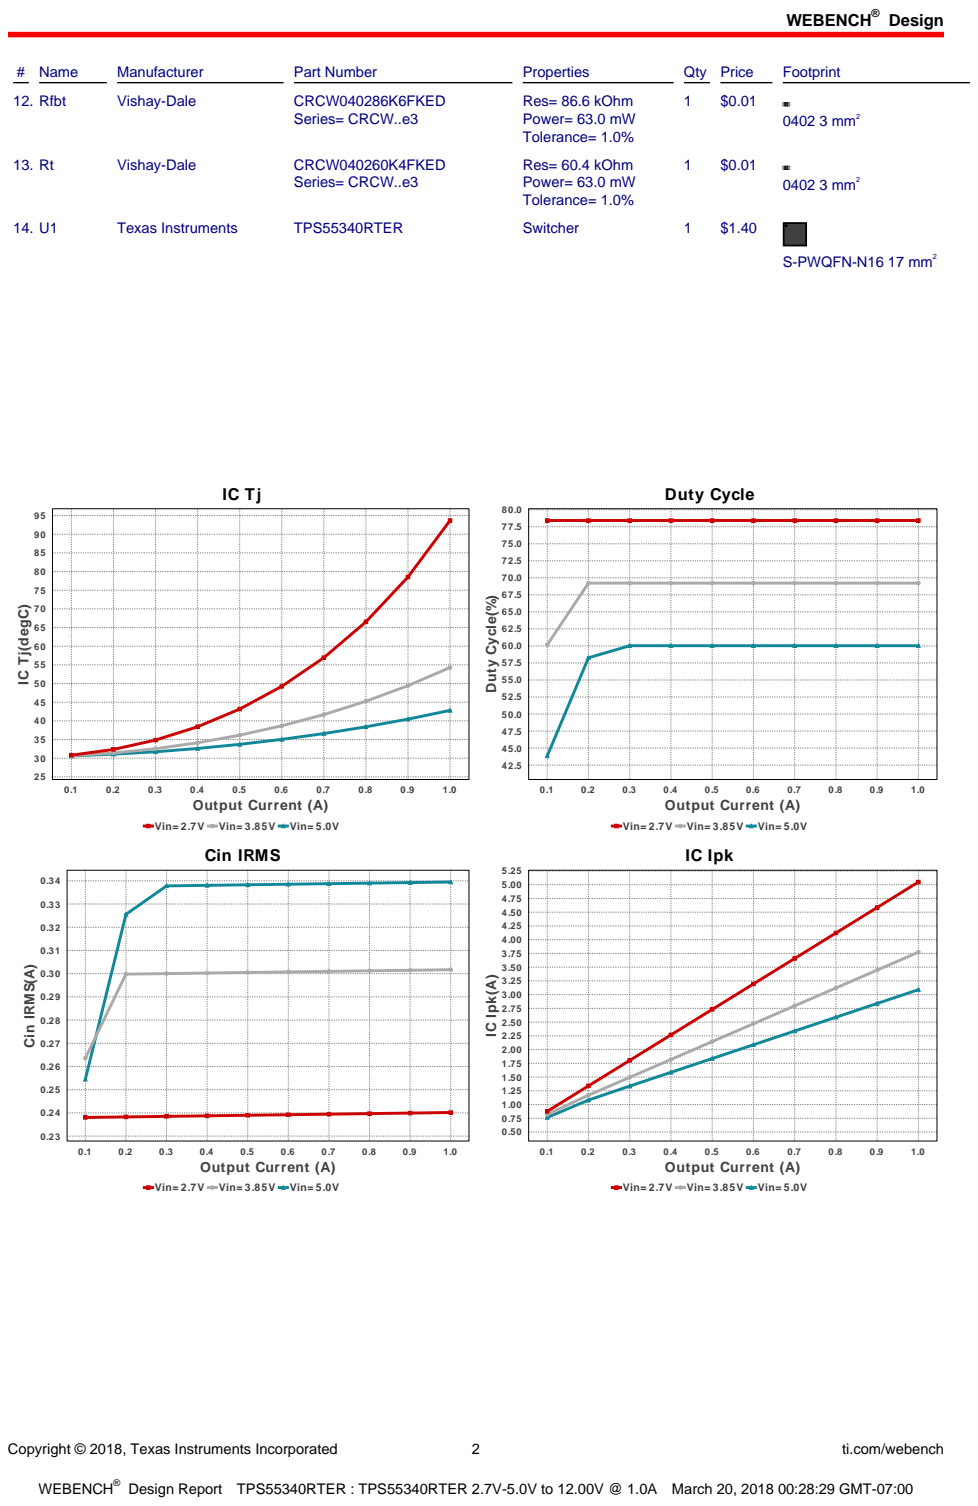
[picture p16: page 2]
Design; Copyright © 2018, Texas Instruments Incorporated; ti.com/webench; # Name; Manufacturer; Part Number; Properties; Qty Price; Footprint; 12. Rfbt; Vishay-Dale; CRCW040286K6FKED; Series= CRCW..e3; Res= 86.6 kOhm Power= 63.0 mW Tolerance= 1.0%; 0402 3 mm²; CRCW040260K4FKED; Res= 60.4 kOhm Power= 63.0 mW Tolerance= 1.0%; Texas Instruments; TPS55340RTER; Switcher; S-PWQFN-N16 17 mm²; 1.0 Output Current (A); Duty Cycle; Duty Cycle(%); Cin IRMS(A); IC Ipk; IC Ipk(A)

IC Tj(degC)

Vin= 2.7V Vin= 3.85V Vin= 5.0V
Cin IRMS

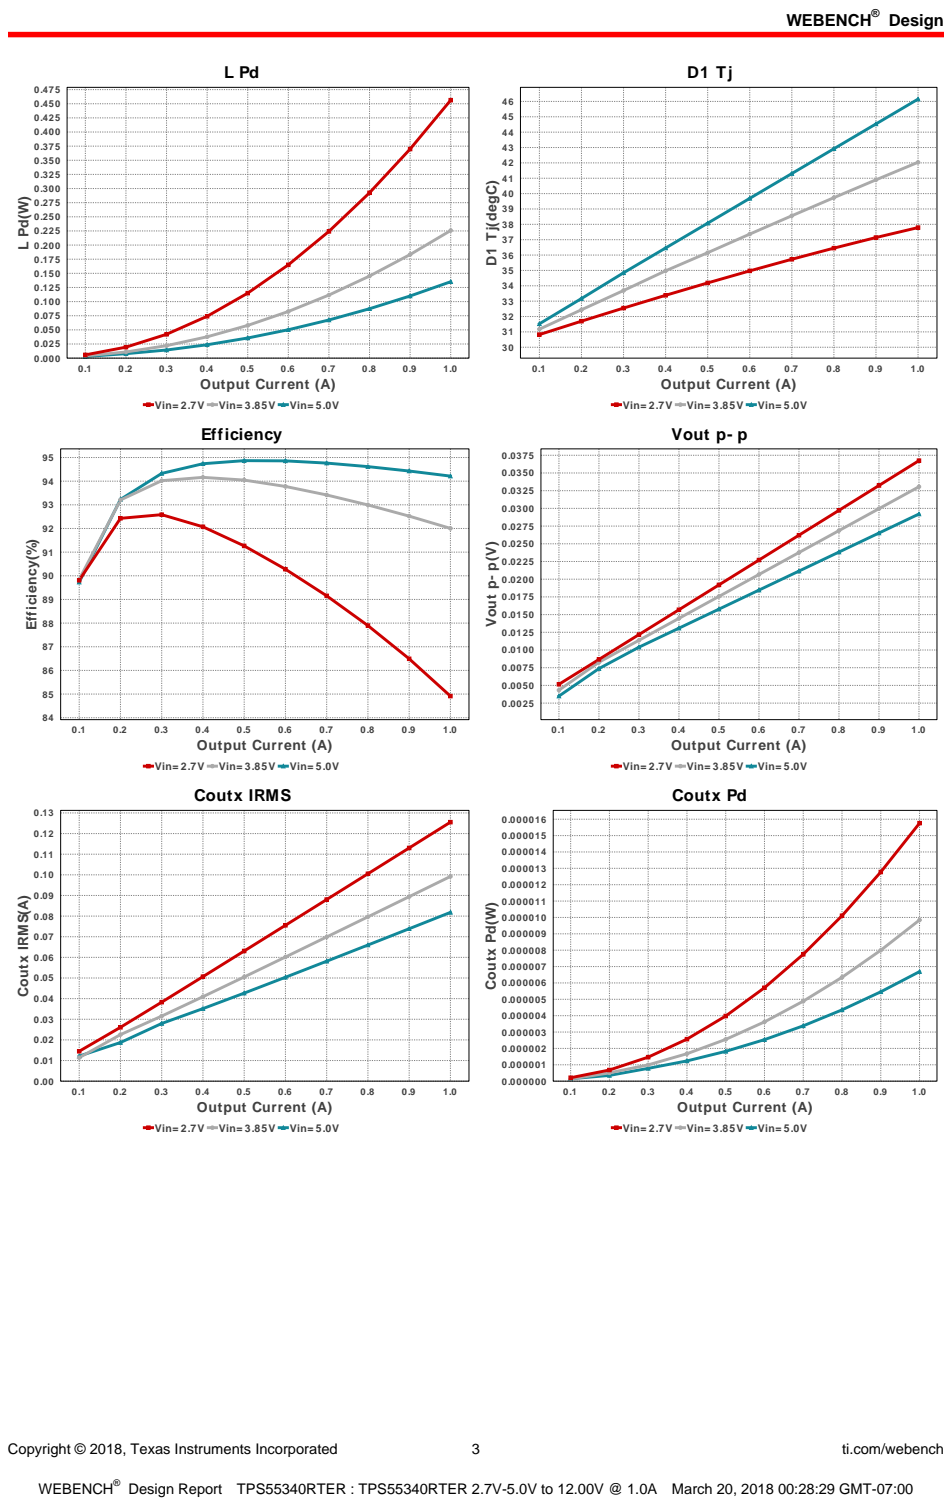
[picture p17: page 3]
Copyright © 2018, Texas Instruments Incorporated; ti.com/webench; 1.0 Output Current (A); D1 Tj(degC); Efficiency(%); Vout p- p(V); Coutx IRMS(A); Coutx Pd(W)

Vin= 2.7V Vin= 3.85V Vin= 5.0V
Efficiency

Vout p- p

Coutx IRMS

Coutx Pd

Copyright © 2018, Texas Instruments Incorporated; ti.com/webench; M Iavg; 1.0 Output Current (A); M Iavg(A); Cin Pd; Cin Pd(W); Cout Pd(W); M Vds Act(V); M Irms; M Irms(A); Pout; Pout(W)

Vin= 2.7V Vin= 3.85V Vin= 5.0V
Cout Pd

M Vds Act

Copyright © 2018, Texas Instruments Incorporated; ti.com/webench; Iin Avg; 1.0 Output Current (A); Iin Avg(A); Total Pd; Total Pd(W); Cout IRMS(A); L Ipp; L Ipp(A); Diode Pd(W)

Vin= 2.7V Vin= 3.85V Vin= 5.0V
Cout IRMS

Diode Pd

Copyright © 2018, Texas Instruments Incorporated; ti.com/webench; Loop Response; Gain Phase + 180; 100,000 Frequency; Gain(dB); Phase + 180(degree); Operating Values; Name; Value; Category; Description; 1. Cin IRMS; Current; Input capacitor RMS ripple current; 2. Cout IRMS; Output capacitor RMS ripple current; 3. Coutx IRMS; Output capacitor_x RMS ripple current; 4. IC Ipk; Peak switch current in IC; 5. Iin Avg; Average input current; 6. L Ipp; Peak-to-peak inductor ripple current; 7. M Iavg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

resistors if applicable

Copyright © 2018, Texas Instruments Incorporated | 7 | ti.com/webench

## Design Assistance

1. TPS55340 Product Folder : http://www.ti.com/product/TPS55340 : contains the data sheet and other resources.

Texas Instruments' WEBENCH simulation tools attempt to recreate the performance of a substantially equivalent physical implementation
of the design. Simulations are created using Texas Instruments' published specifications as well as the published specifications of other device manufacturers. While Texas Instruments does update this information periodically, this information may not be current at the time the simulation is built. Texas Instruments does not warrant the accuracy or completeness of the specifications or any information contained therein. Texas Instruments does not warrant that any designs or recommended parts will meet the specifications you entered, will be suitable for your application or fit for any particular purpose, or will operate as shown in the simulation in a physical implementation. Texas Instruments does not warrant that the designs are production worthy.
You should completely validate and test your design implementation to confirm the system functionality for your application prior to production.
Use of Texas Instruments' WEBENCH simulation tools is subject to Texas Instruments' Site Terms and Conditions of Use. (http://www.ti.com/corp/docs/legal/termsofuse.shtml) Prototype boards based on WEBENCH created designs are provided AS IS without warranty of any kind for evaluation and testing purposes and are subject to the terms of the Evaluation License Agreement. (http://www.ti.com/corp/docs/legal/termsofuse_estore.shtml)

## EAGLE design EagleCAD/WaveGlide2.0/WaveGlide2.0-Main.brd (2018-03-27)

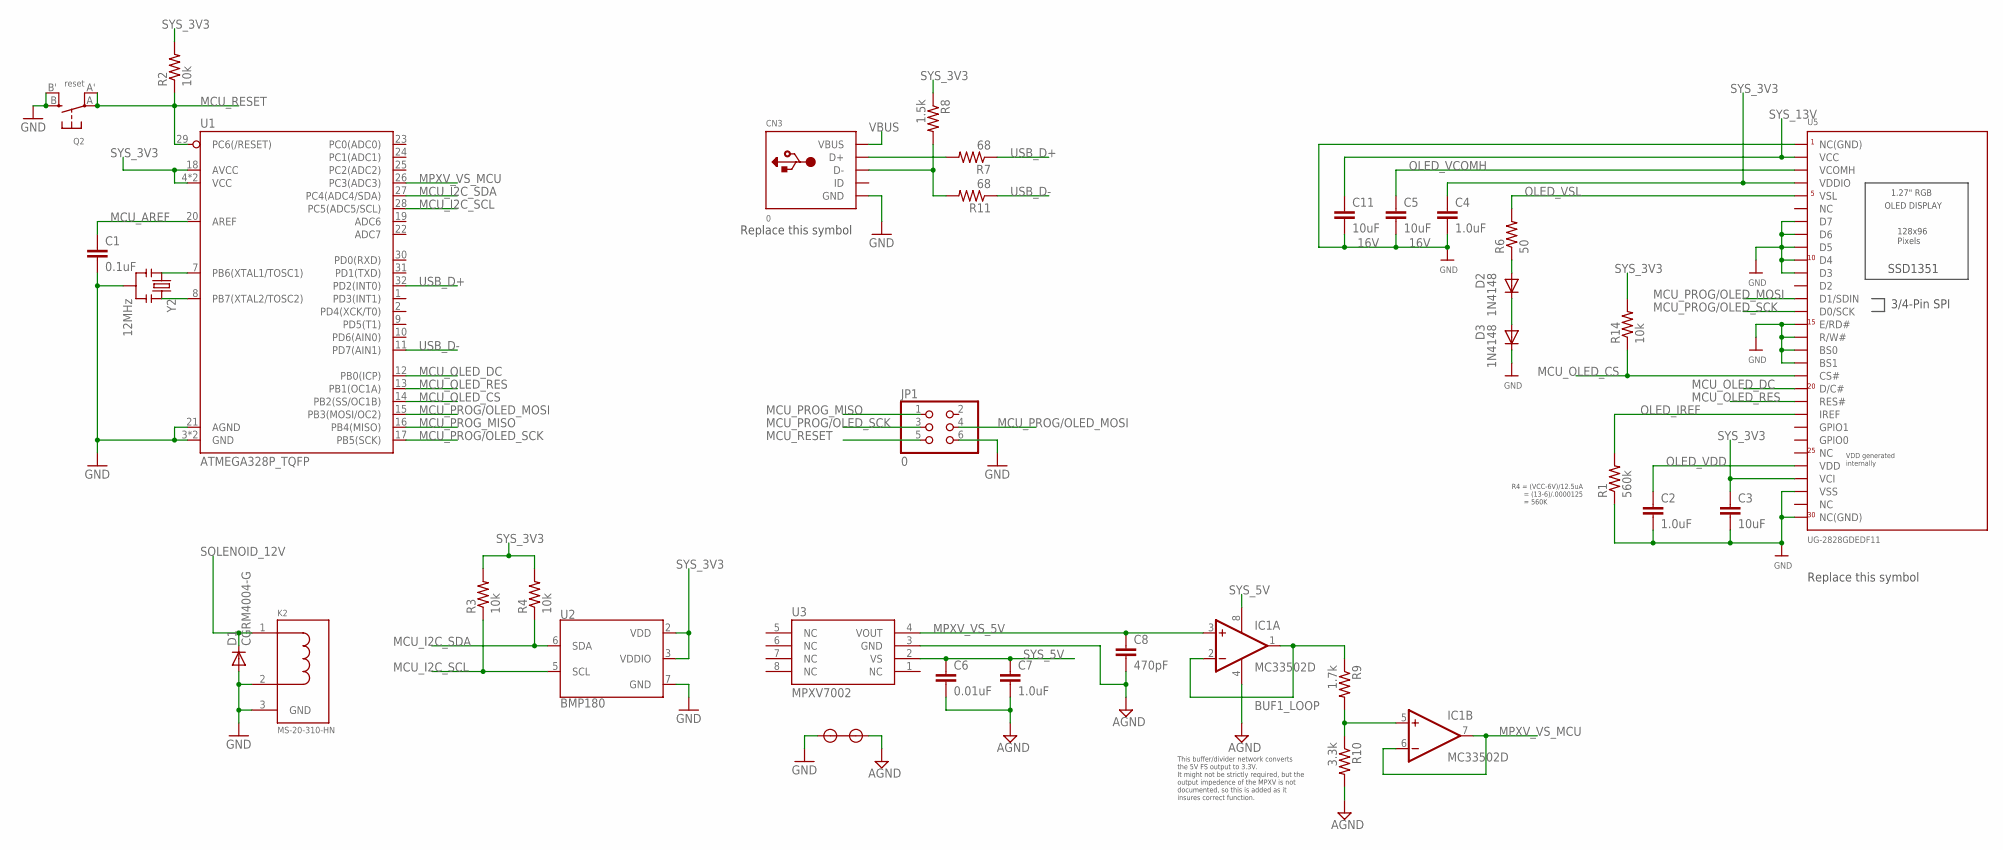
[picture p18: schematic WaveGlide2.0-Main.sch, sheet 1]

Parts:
C1: 0.1uF; C0805
C2, C4, C7: 1.0uF; C0805
C3, C5, C11: 10uF; C0805
C6: 0.01uF; C0805
C8: 470pF; C0805
CN3: 0; 4UCONN_20329
D1: CGRM4004-G; SOD-123_MINI-SMA
D2: 1N4148; SOD323-W; MPN MBRD835LT4G
D3: 1N4148; SOD323-W
IC1: MC33502D; SO08
JP1: 0; 2X03
K2: MS-20-310-HN
Q2: reset; BTN_KMR2_4.6X2.8
R1: 560k; R0603
R2, R3, R4, R14: 10k; R0603
R6: 50; R0603
R7, R11: 68; R0603
R8: 1.5k; R0603
R9: 1.7k; R0603
R10: 3.3k; R0603
U1: ATMEGA328P_TQFP; TQFP32-08; MPN TPS55340RTER
U2: BMP180
U3: MPXV7002
U5: UG-2828GDEDF11; FPC_XF2M-3015-1A
U$2: SHORT
Y2: 12MHz; RESONATOR-SMD

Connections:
AGND: C6.2, C7.2, C8.2, IC1.4 (V-), R10.2, U3.3 (GND), U$2.P$2
BUF1_LOOP: IC1.1 (OUT), IC1.2 (-IN), R9.1
D+1: CN3.D+, R7.2
D-1: CN3.D-, R8.2, R11.2
GND: C1.2, C2.2, C3.2, C4.2, C5.2, C11.2, CN3.BASE@1 (GND), CN3.BASE@2 (GND), CN3.GND, CN3.SPRT@1 (GND), CN3.SPRT@2 (GND), CN3.SPRT@3 (GND), CN3.SPRT@4 (GND), D1.A, D3.C, JP1.6, K2.2 (VR), K2.3 (GND), Q2.B (S), Q2.B' (S1), R1.1, U1.3 (GND), U1.5 (GND), U1.21 (AGND), U2.7 (GND), U5.P$1 (NC(GND)), U5.P$3 (VSS), U5.P$13 (BS1), U5.P$14 (BS0), U5.P$15 (R/W#), U5.P$16 (E/RD#), U5.P$20 (D3), U5.P$21 (D4), U5.P$22 (D5), U5.P$23 (D6), U5.P$24 (D7), U5.P$30 (NC(GND)), U$2.P$1, Y2.2; also elsewhere on the board
MCU_AREF: C1.1, U1.20 (AREF)
MCU_I2C_SCL: R3.1, U1.28 (PC5(ADC5/SCL)), U2.5 (SCL)
MCU_I2C_SDA: R4.1, U1.27 (PC4(ADC4/SDA)), U2.6 (SDA)
MCU_OLED_CS: R14.1, U1.14 (PB2(SS/OC1B)), U5.P$12 (CS#)
MCU_OLED_DC: U1.12 (PB0(ICP)), U5.P$11 (D/C#)
MCU_OLED_RES: U1.13 (PB1(OC1A)), U5.P$10 (RES#)
MCU_PROG/OLED_MOSI: JP1.4, U1.15 (PB3(MOSI/OC2)), U5.P$18 (D1/SDIN)
MCU_PROG/OLED_SCK: JP1.3, U1.17 (PB5(SCK)), U5.P$17 (D0/SCK)
MCU_PROG_MISO: JP1.1, U1.16 (PB4(MISO))
MCU_RESET: JP1.5, Q2.A, Q2.A' (P1), R2.1, U1.29 (PC6(/RESET))
MPXV_VS_5V: C8.1, IC1.3 (+IN), U3.4 (VOUT)
MPXV_VS_MCU: IC1.6 (-IN), IC1.7 (OUT), U1.26 (PC3(ADC3))
unnamed: D2.C, D3.A
unnamed: D2.A, R6.1
unnamed: IC1.5 (+IN), R9.2, R10.1
unnamed: U1.7 (PB6(XTAL1/TOSC1)), Y2.1
unnamed: U1.8 (PB7(XTAL2/TOSC2)), Y2.3
OLED_IREF: R1.2, U5.P$9 (IREF)
OLED_VCOMH: C5.1, U5.P$28 (VCOMH)
OLED_VDD: C2.1, U5.P$5 (VDD)
OLED_VSL: R6.2, U5.P$26 (VSL)
SOLENOID_12V: D1.C, K2.1 (VS); also elsewhere on the board
SYS_3V3: C3.1, C4.1, R2.2, R3.2, R4.2, R8.1, R14.2, U1.4 (VCC), U1.6 (VCC), U1.18 (AVCC), U2.2 (VDD), U2.3 (VDDIO), U5.P$4 (VCI), U5.P$27 (VDDIO); also elsewhere on the board
SYS_5V: C6.1, C7.1, IC1.8 (V+), U3.2 (VS); also elsewhere on the board
SYS_13V: C11.1, U5.P$29 (VCC); also elsewhere on the board
USB_D+: R7.1, U1.32 (PD2(INT0))
USB_D-: R11.1, U1.11 (PD7(AIN1))
VBUS: CN3.VBUS

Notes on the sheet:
R4 = (VCC-6V)/12.5uA = (13-6)/.0000125 = 560K
VDD generated internally
This buffer/divider network converts the 5V FS output to 3.3V. It might not be strictly required, but the output impedence of the MPXV is not documented, so this is added as it insures correct function.
Replace this symbol

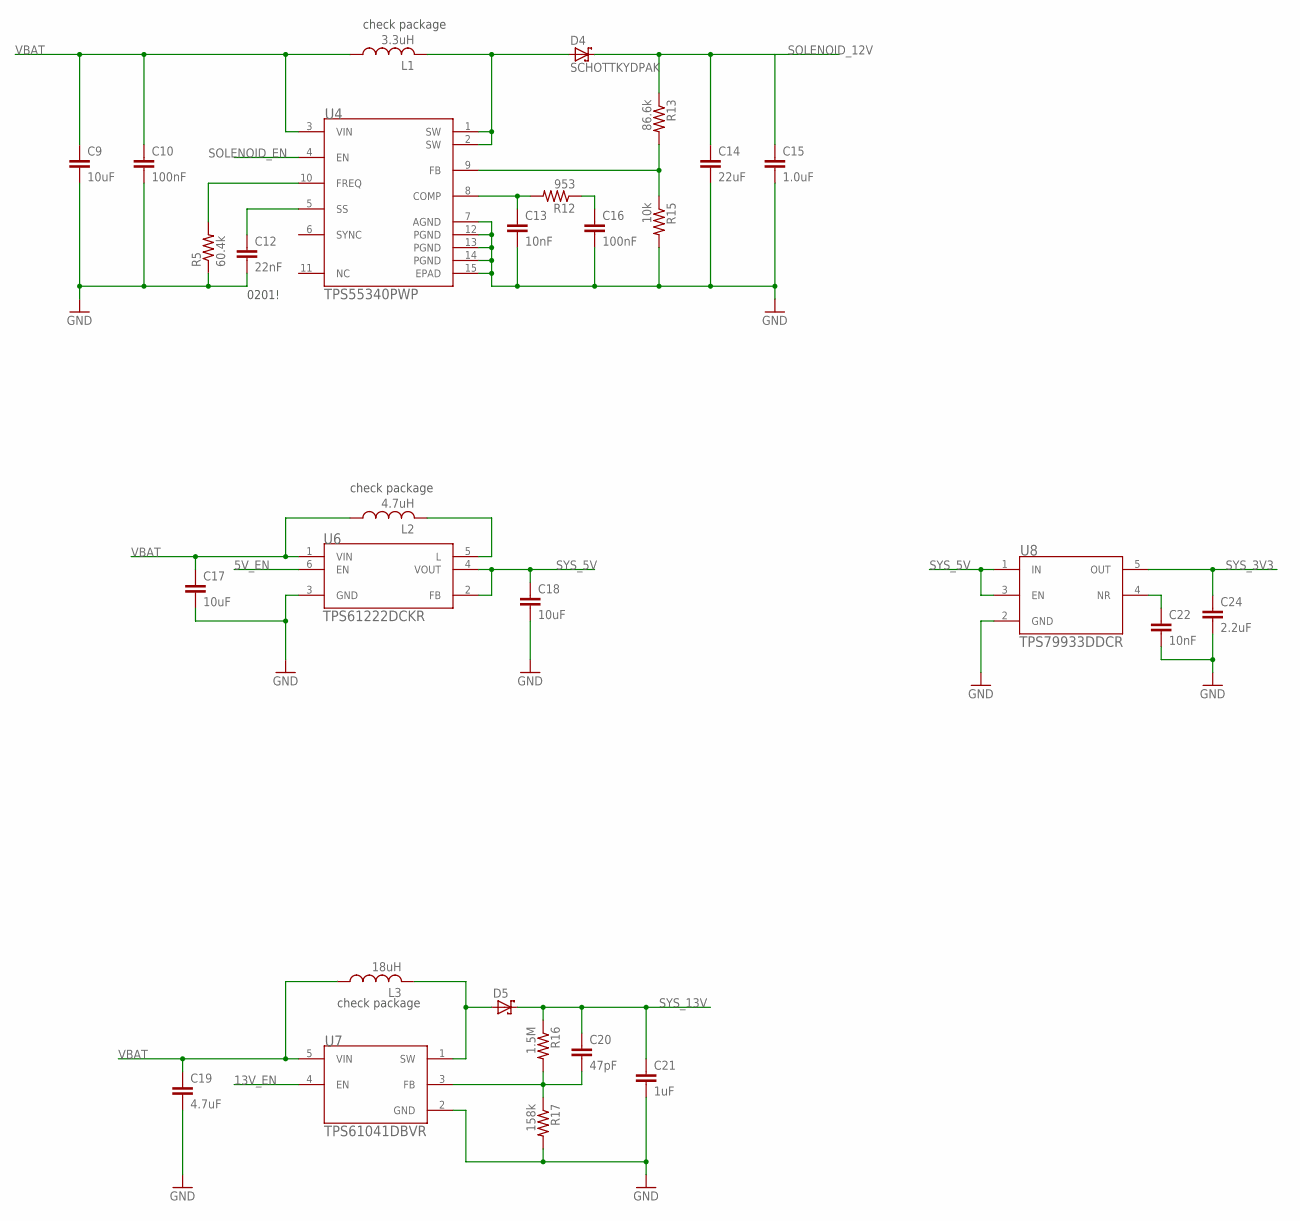
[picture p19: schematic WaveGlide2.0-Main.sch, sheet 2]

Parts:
C9: 10uF; C0805; MPN GRM219R61A106KE44D
C10: 100nF; C0805; MPN CC0805KRX7R8BB104
C12: 22nF; C0402; MPN GRM155R60J223KA01D
C13: 10nF; C0805; MPN GCM2195C1H103JA16D
C14: 22uF; C1210; MPN GRM32ER61C226ME20L
C15: 1.0uF; C0805; MPN EMK107B7105KA-T
C16: 100nF; C0805; MPN 08053C104JAZ2A
C17: 10uF; C0805; MPN GRM21BR60J106ME19L
C18: 10uF; C0805; MPN C0805C106K8PACTU
C19: 4.7uF; C0603; MPN GRM188R60J475KE19D
C20: 47pF; C0603; MPN 06035A470KAT2A
C21: 1uF; C0805; MPN GMK212B7105KG
C22: 10nF; C0402; MPN GRM033R70J103KA01D
C24: 2.2uF; C0402; MPN JMK105BJ225MV-F
D4: SCHOTTKYDPAK; D-PAK_TO252AA
D5: SCHOTTKYSOT-123; SOD-123_MINI-SMA
L1: 3.3uH; L4532P; MPN XAL5030-332MEB
L2: 4.7uH; L4035M; MPN LQM2HPN4R7MGCL
L3: 18uH; L4035M; MPN LPS4018-183MRB
R5: 60.4k; R0603; MPN CRCW060360K4FKEA
R12: 953; R0603; MPN CRCW0603953RFKEA
R13: 86.6k; R0603; MPN CRCW060386K6FKEA
R15: 10k; R0805; MPN RR1220P-103-D
R16: 1.5M; R0603; MPN CRCW06031M50FKEA
R17: 158k; R0603; MPN CRCW0603158KFKEA
U4: TPS55340PWP; PWP14
U6: TPS61222DCKR; DCK6
U7: TPS61041DBVR; DBV5
U8: TPS79933DDCR; DDC5

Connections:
5V_EN: U6.6 (EN)
13V_EN: U7.4 (EN)
GND: C9.2, C10.2, C12.2, C13.2, C14.2, C15.2, C16.2, C17.2, C18.2, C19.2, C21.2, C22.2, C24.2, R5.1, R15.2, R17.2, U4.7 (AGND), U4.12 (PGND), U4.13 (PGND), U4.14 (PGND), U4.15 (EPAD), U6.3 (GND), U7.2 (GND), U8.2 (GND); also elsewhere on the board
unnamed: D5.A, L3.2, U7.1 (SW)
SOLENOID_12V: C14.1, C15.1, D4.4 (C), R13.1; also elsewhere on the board
SOLENOID_EN: U4.4 (EN)
SYS_3V3: C24.1, U8.5 (OUT); also elsewhere on the board
SYS_5V: C18.1, U6.2 (FB), U6.4 (VOUT), U8.1 (IN), U8.3 (EN); also elsewhere on the board
SYS_13V: C20.1, C21.1, D5.C, R16.1; also elsewhere on the board
TPS55340_COMP: C13.1, R12.2, U4.8 (COMP)
TPS55340_FB: R13.2, R15.1, U4.9 (FB)
TPS55340_FB1: C20.2, R16.2, R17.1, U7.3 (FB)
TPS55340_FREQ: R5.2, U4.10 (FREQ)
TPS55340_SS: C12.1, U4.5 (SS)
TPS55340_SW: D4.1 (A), D4.3 (A), L1.2, U4.1 (SW), U4.2 (SW)
TPS61222_L: L2.2, U6.5 (L)
TPS66340_COMP1: C16.1, R12.1
TPS79933_NR: C22.1, U8.4 (NR)
VBAT: C9.1, C10.1, C17.1, C19.1, L1.1, L2.1, L3.1, U4.3 (VIN), U6.1 (VIN), U7.5 (VIN)

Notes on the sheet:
0201!
check package

Board: 2 copper layers, 63 parts (10 on the bottom side), 43 nets, no tracks yet.

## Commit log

2018-03-10 KiCAD CAD
    [WaveGlide2.0.kicad_pcb, WaveGlide2.0.sch]
2018-03-11 Updated docs and part additions
    [WaveGlide2.0-Main.brd, WaveGlide2.0-Main.sch]
2018-03-16 Add OLED ref schematic
2018-03-16 Updated BOM, add more docs
2018-03-16 Updated Schematic
    [WaveGlide2.0-Main.brd, WaveGlide2.0-Main.sch]
2018-03-16 Add MCAD step files
    [BMP180.step, GB-MS-20 + Press Fits v2.step, GB-MS-20 + Press Fits v3.step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]
2018-03-16 Rearrange Docs, add final power components
2018-03-16 TI Ref designs for power
2018-03-17 Start generating schematic
    [WaveGlide2.0-Main.brd, WaveGlide2.0-Main.sch]
2018-03-17 AVR Pocket Reference Board
    [AVR-Pocket-Programmer-v15.brd, AVR-Pocket-Programmer-v15.sch]
2018-03-17 Fix DRC unknown net issues
    [WaveGlide2.0-Main.sch]
2018-03-18 Add buffer divider network, and floorplanning
    [WaveGlide2.0-Main.brd, WaveGlide2.0-Main.sch]
2018-03-20 Add design notes for the 12V boost
2018-03-20 Add BOM management
2018-03-20 Add TPS55340 boost circuit
    [WaveGlide2.0-Main.brd, WaveGlide2.0-Main.sch]
2018-03-20 Death to spaces in paths
    [WaveGlide2.0-Main.brd, WaveGlide2.0-Main.sch]
2018-03-26 Add 5V regulator
    [WaveGlide2.0-Main.brd, WaveGlide2.0-Main.sch]
2018-03-26 Add 13V boost for OLED
    [WaveGlide2.0-Main.brd, WaveGlide2.0-Main.sch]
2018-03-26 Update BOM fix some bad components
    [WaveGlide2.0-Main.brd, WaveGlide2.0-Main.sch]
2018-03-26 Add 3V3 Regulator
    [WaveGlide2.0-Main.brd, WaveGlide2.0-Main.sch]
2018-03-27 Add diodes to power regulators
    [WaveGlide2.0-Main.brd, WaveGlide2.0-Main.sch]
2018-03-27 Floor planning 12V regulator
    [WaveGlide2.0-Main.brd]

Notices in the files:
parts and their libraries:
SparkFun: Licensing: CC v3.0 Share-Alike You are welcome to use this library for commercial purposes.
